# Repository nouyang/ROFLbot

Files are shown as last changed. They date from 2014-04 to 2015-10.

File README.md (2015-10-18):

# Videos

- Lab 1. Wall Find [http://www.youtube.com/watch?v=qMBVbE07Tbg](http://www.youtube.com/watch?v=qMBVbE07Tbg)
- Lab 6. Bulls Eye [https://www.youtube.com/watch?v=fWD04yWnOBU](https://www.youtube.com/watch?v=fWD04yWnOBU)
- Lab 8. Head with potentiometer[ http://www.youtube.com/watch?v=5r9yhMpieDI](http://www.youtube.com/watch?v=5r9yhMpieDI) (position control with motor pot and external pot shown)
- Lab 9. Head with photodiode[ http://www.youtube.com/watch?v=XeEDuTtJMeo](http://www.youtube.com/watch?v=XeEDuTtJMeo)
- Lab 10. Robot with Head [https://www.youtube.com/watch?v=qIvbUR9brPU](https://www.youtube.com/watch?v=qIvbUR9brPU), Rotational Only: [https://www.youtube.com/watch?v=JFF51LcxRAY](https://www.youtube.com/watch?v=JFF51LcxRAY)
- Lab 13. Parking (a) overhead shot (to view any wall-following wobble) [https://www.youtube.com/watch?v=gBMiRD48gqk](https://www.youtube.com/watch?v=gBMiRD48gqk)
     (b) with view of screen / position estimation bars [https://www.youtube.com/watch?v=aKtX0ltPgmw](https://www.youtube.com/watch?v=aKtX0ltPgmw)

# Quickstart
If you have the robot already, simply:

1. Install [lib601](https://github.com/mitocw/mit-6.01-NarwhalEdu-robot/blob/master/lib601.tar.gz) from the 6.01 website.
2. Then replace **/usr/local/lib/python2.7/dist-packages/soar/outputs/pioneer.py** with the NarwhalEdu [pioneer.py](https://github.com/mitocw/mit-6.01-NarwhalEdu-robot/blob/master/code/pioneer.py) 
3. Connect the xbee to the computer
4. Open a terminal and run "dmesg | tail". Note which port is connected -- usually /dev/ttyUSB0 or /dev/ttyACM0.
5. Inside pioneer.py (must be admin to edit this file), edit the line appropriately settings.SERIAL_PORT_NAME = "/dev/ttyUSB1"
6. Run soar from the terminal
7. Click **pioneer** to connect to the robot. If the button stays depressed for a few seconds, that means that you have the right serial port but are having issues connecting to the robot. If it comes depressed right away, check that you edited pioneer.py with the appropriate serial port. If it's connected, it should look like below:

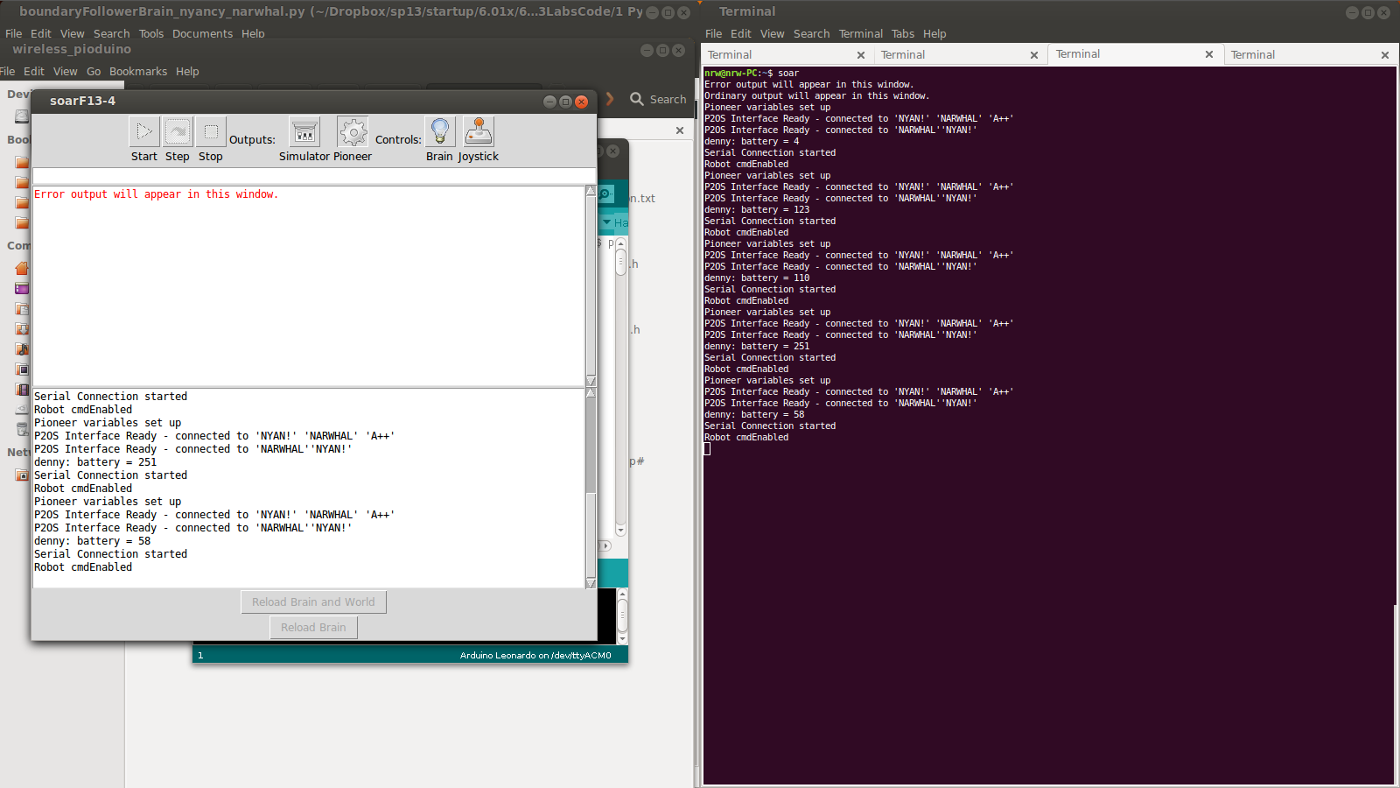
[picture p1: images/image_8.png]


8. If you continue experiencing issues connecting to the robot: hit reset and wait a few seconds (the xbees appear to take a second or two to initialize). Second, try turning the robot on and off. Try replugging the xbee into your computer. Try restarting SOAR. 
9. After it's connected, hit **brain** and load the appropriate brain python file you have written.
10. Hit the square STOP button to stop running the program, and then Reload Brain **and World **if you are going to be moving the robot.

Note:
11. Watch out if the robot ever stops responding or is behaving oddly -- is it still connected to SOAR? and if so, are the batteries low?
12. Other things that are good to check initially -- are the left and right motors mapped in code correctly, are the directions of each motor mapped correctly, are the IR sensors mapped correctly
13. Debugging tip: Robot can be put on top of two wire spools with the casters sitting inside the spools to debug the motors without having it drive all over the place

# Introduction

MIT Office of Digital Learning (ODL) contracted NarwhalEdu to create a
replacement for the robots used in 6.01 as of 2013. 

As of 2013, the Pioneer-DX robots are used, with a head consisting of a
lego motor, a custom 3d-printed chassis, and a custom PCB with two
photodiodes on it.

The motivation for our work was twofold:
1. A smaller robot would allow students to do labs at home
2. A cheaper robot would be more reasonable for online students

In this section, a brief retrospective on the work accomplished and
lessons learned follows, and we end with thoughts about future work. In
the appendix, one may find the proposal we submitted to the ODL.

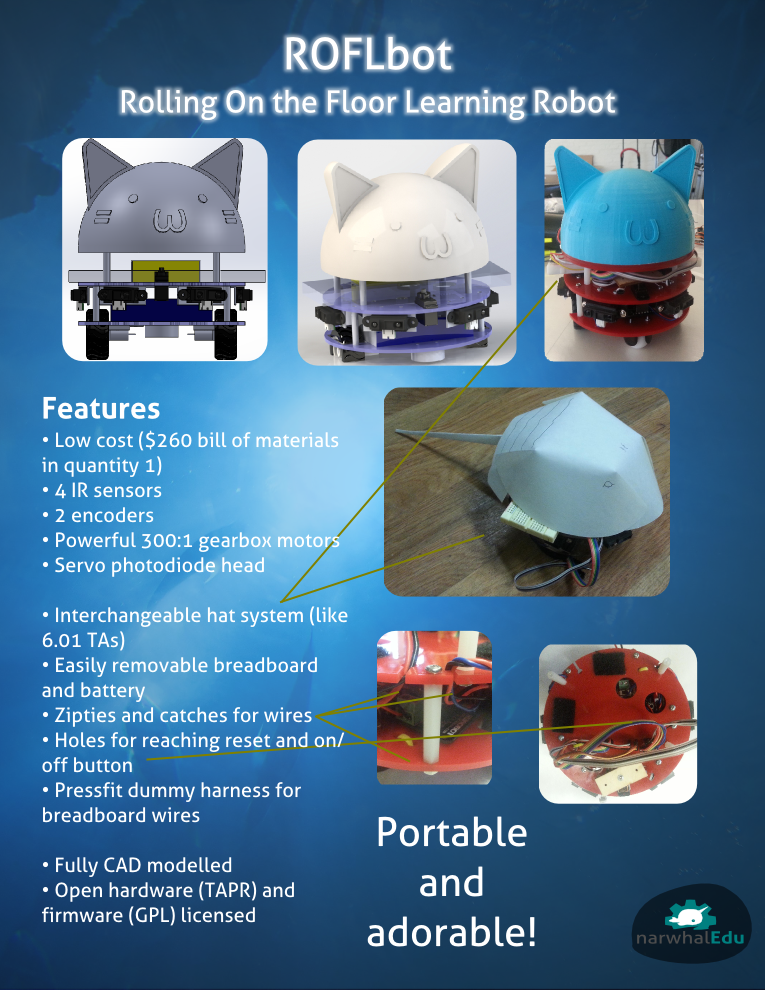
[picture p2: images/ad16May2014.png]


## Who are we?
We’re two engineers from MIT helping students fall in love with
engineering by showcasing its creative side. We're passionate about
increasing the number and diversity of students interested in
engineering around the world, and we hope to bring people together over
the awesome projects that they build.

NarwhalEdu was founded in August 2013 by two MechE '13s: Cappie Pomeroy
and Nancy Ouyang, and ran a successful kickstarter for its first course,
"[Robots, Drawing, and Engineering: An Online
Course](https://www.kickstarter.com/projects/narwhaledu/robots-drawing-and-engineering-an-online-course)," in December 2013.

## Timeline

2013

9/9 Proposal submitted

10/9 Supplies ordered as per invoice

  10/15 PO setup for our work by the ODL

  10/16 Invoice submitted by NarwhalEdu

11/11 Ordered the poorly-documented DFRobot MiniQ robot

  11/17 Check cut

  11/22 Check cashed

2014

1/31 First meeting with Prof. Chuang

2/4 Order gyros, IR distance sensors, Romeo controller board, optical encoders (3.3V by mistake)

2/17 Order 5V optical encoders

2/26 Order 3.3V optical encoders, because they actually work

3/31 Order 300:1 motors, more IR sensors

4/25 1 layer version

5/16 Demo of 2 layer cat head version 

## Summary of Work
In 2013, we evaluated different CPUs, distance sensors, chassis, motors,
and odometry systems. 

We discovered the $79 MiniQ robot, which seemed perfect for our needs,
though it was poorly documented. It was, of course, too good to be true.
The critical two factors were sub-optimal distance and odometry sensing.
In short, we could rig left and right distance sensing, but the sensors
were definitely designed for proximity and not distance sensing. Our
robot was also moving slow enough that we really needed to measure
rotations of the motor, not of the output after the gearbox. (For more
details, see Side Note: Sensors below). However, it did give us the
basis to develop our own robot from scratch and a sense of at what cost
robots could be sold.

As of our first meeting:

CPU: We decided on using Arduino for free and easy-to-use cross-platform
programming toolchain. There was a motor controller - arduino-compatible
board, the Romeo controller, that we found sufficient for our needs.
Distance: We decided on the Sharp IR sensors, since they have a
relatively linear response curve and I knew there was 2.007 code we
could use for them.

Odometry and Chassis: We decided on the pololu round chassis with
high-quality 100:1 gearmotors, since pololu sells them with extended
shafts so that the optical encoders can mount to them. We investigated
gyros but did not end up needing them.

* Note: DFRobot does not sell [knockoff] extended motor brackets that
  cover the gearbox, their "extended" ones are the equivalent of pololu
normal ones, so hair will tend to get caught in them. 

We struggled a lot with the optical encoders. They need thin wires or
else the pads get heat-damaged and fall off. We found servo wires
sufficient for this purpose. Additionally, we bought 3.3V ones by
accident, then bought 5V ones after desoldering a lot of pads, and after
troubleshooting realized that the 5V ones did not generate large enough
signal swing at 5V to trigger the interrupts, but the 3.3 V ones did.

Around this time we also began exploring wireless options, as we found
that the cable to the computer significantly impacted evaluation of the
odometry. Although the previous MiniQ was wirelessly programmable, the
leonardo Romeo board was not. However, this was fine because we learned
that we only needed to wirelessly transmit data. We started with the
xbee, which was the most expensive but the easiest to use given the
pre-existing slot on the romeo. We struggled a lot with the xbee.
Ultimately, a combination of fixing code errors and learning about the
ins and outs of xbees allowed us to create a reliable wireless robot.
(115200 does not exist on the xbee! We ended up using 19200 to avoid any
weird xbee bad rate issues.)

Further work was done to determine that only three IR sensors were
needed to complete the parking lab, however, they had to be
asymmetrically placed. We struggled with the parking lab before
realizing that the real world needed to match the ideal world given to
the robot fairly closely.

### Side Note: MiniQ Documentation
It has
* atmega328p
* cleverly cheap wheel encoders
* spot for an xbee or for the DFrobot Wireless Programming Kit, which
  allows you to wirelessly upload programs
* USB programmable
* a piezo
* lots of LEDs
* pushbuttons
* IRM881T IR receiver that could respond to a keychain remote
* a left and right photoresistor
* two IR LEDs
* 4x ITR2001 optointerupters on the bottom for line-following

### Side Note: Sensors
The IR receiver was a 38kHz receiver. It has a slightly varying response
depending on the strength of the signal received, but in a non-linear
and generally awkward fashion. Conceivably, we could have beeped our two
IR LEDs at 38kHz (alternating, since we only have one receiver, and we
keep track of which are left and which are right) and tried to derive
the distance based on the number of interrupts the IR receiver generates
(DFRobot does provide some sample code that allows you to control the
robot with the remote supplied with the robot), or try short bursts that
get longer and longer until we receive an interrupt, or chirp out a
varying frequency from 36 to 42 kHz and see where we stop getting
interrupts. We could use the photoresistors, but they have slow response
times and wouldn't allow us to modulate at a reasonable frequency so
that we could easily filter out ambient IR. All-in-all, rather
inconvenient, if amazingly cheap. 

We ended up going with the Sharp IR sensors.

The encoder system, developed most likely by pololu originally, worked
thusly: for each wheel, there were two IR20510 light reflection switches
mounted to the chassis. The wheel hub had 12 notches, and as each notch
passed over the switches, it triggered an interrupt. Between the two
reflection switches, this allows the user to treat this system as a
quadrature encoder and be able to detect roughly the speed and whether
the wheel was turning forward or backward. This gives a maximum linear
sensitivity of 3mm. 

See
[http://www.pololu.com/product/1217/resources](http://www.pololu.com/product/1217/resources)
for more information.

This system is cheap and doesn't require any calibration (easy for the
user to assemble), but too low-resolution for our purposes, since we're
always running at low speed. We had difficulty getting the robot to
drive slowly in a straight line with our PID loop. It was limited to 48
ticks per revolution of the wheel, and we had a 100:1 gearbox going at
the time. Ultimately we decided on optical encoders that attached to the
motor shaft directly.

## Details
For more details, see our report on Jan 31, 2014 and on March 11, 2014
in the appendix.

## Future Work
16 May 2014

2 layer robot with interchangeable head system finished.
Immediate fixes recommened: add more holes on top layer to allow access
to motor block terminals on romeo with a screwdriver, lower nut or
otherwise more clearance for USB on romeo (front caster interferes at
the moment), fix fudge factor known as
encodermillimeterconversionfactor (in localization.h) as the motors are
running at lipo voltage ~8v instead of the 5v we thought they were
running at.

25 March 2014

Future work lies in resolving where the breadboard should go and
building a better jig for the head than hot glue, as well as resolving
the photodiode wires into a connector. In the short-term this can
involve a two-layer lasercut chassis with the controller on the bottom
and the breadboard on top. In the future we recommend building the romeo
controller into a custom PCB that serves as the bottom layer and allows
the breadboard layer to be attached with standoffs. This shrinks the
diameter required. Additionally, the optical encoders are finicky in
terms of assembly (they require an oscilloscope to calibrate) and we
hope to replace them with a future product of pololu, magnetic encoder
disks with hall effect sensors that can be integrated into the PCB.
Given a large enough order, a factory can directly create the
control-board-less servo with two tails.

In the future, we recommend better communication between the 6.01 staff
and contractors. Most of our questions were answered by former students
we knew.

13 June 2014
Future work will probably lie in migrating away from the optical
encoders, which are really annoying to calibrate. Additionally, we need
to pick a license and also publish the hardware and firmware to a
publicly accessible repository. The code examples need to be refined,
especially roverBrain, to work consistently. A better holder (hinged)
for the interchangeable heads would be great as well.

## BoM
All prices in USD and as of March 2014.
                                             
<table>
  <tr>
    <td>Name</td>
    <td>Total Cost</td>
    <td></td>
    <td>Product Name</td>
    <td>URL</td>
  </tr>
  <tr>
    <td>Custom Lasercut Chassis (based on pololu)</td>
    <td>$7.95</td>
    <td>pololu</td>
    <td>#1507 Pololu 5" Robot Chassis RRC04A Transparent Light-Blue</td>
    <td>http://www.pololu.com/product/1507</td>
  </tr>
  <tr>
    <td>Lipo Battery Connector</td>
    <td>$0.99</td>
    <td>pololu</td>
    <td>JST RCY Plug with 10cm Leads, Male</td>
    <td>http://www.pololu.com/product/2181</td>
  </tr>
  <tr>
    <td>Lipo Battery</td>
    <td>$4.65</td>
    <td>hobbyking</td>
    <td>Turnigy 1000mAh 2S 20C Lipo Pack</td>
    <td>http://www.hobbyking.com/hobbyking/store/__9170__Turnigy_1000mAh_2S_20C_Lipo_Pack.html</td>
  </tr>
  <tr>
    <td>4x Sharp IR Sensor</td>
    <td>$39.80</td>
    <td>pololu</td>
    <td>#136 Sharp GP2Y0A21YK0F Analog Distance Sensor 10-80cm</td>
    <td>http://www.pololu.com/product/136</td>
  </tr>
  <tr>
    <td>3x Sharp IR mount</td>
    <td>$15.00</td>
    <td>robotmesh</td>
    <td>Sharp IR Sensor Mounting Bracket-GP2Y0A21/GP2Y0A02YK</td>
    <td>http://www.robotmesh.com/sharp-ir-sensor-mounting-bracket-gp2y0a21-gp2y0a02yk?___SID=U</td>
  </tr>
  <tr>
    <td>10x bolts for IR mount, mcu</td>
    <td>$1.63</td>
    <td>mcmaster</td>
    <td>Zinc-pltd Stl Pan Head Phillips Machine Screw, 4-40 Thread, 1/2" Length x 100</td>
    <td>http://www.mcmaster.com/?error_redirect=true#90272a110</td>
  </tr>
  <tr>
    <td>10x nuts for IR mount, mcu</td>
    <td>$0.81</td>
    <td>mcmaster</td>
    <td>Zinc-plated Steel Machine Screw Hex Nut, 4-40 Thread Size, 1/4" Width, 3/32" Height x 100</td>
    <td>http://www.mcmaster.com/?error_redirect=true#90480A005</td>
  </tr>
  <tr>
    <td>2x 300:1 Gearmotor</td>
    <td>$33.90</td>
    <td>pololu</td>
    <td>#2218 298:1 Micro Metal Gearmotor HP with Extended Motor Shaft</td>
    <td>http://www.pololu.com/product/2218</td>
  </tr>
  <tr>
    <td>42x19mm Wheel, pair</td>
    <td>$3.85</td>
    <td>robotmesh</td>
    <td>Wheel 42x19mm (Pair)</td>
    <td>http://www.robotmesh.com/wheel-42x19mm-pair</td>
  </tr>
  <tr>
    <td>Extended Motor Bracket, Pair</td>
    <td>$2.99</td>
    <td>pololu</td>
    <td>#1089 Pololu Micro Metal Gearmotor Bracket Extended Pair</td>
    <td>http://www.pololu.com/product/1089</td>
  </tr>
  <tr>
    <td>2x Optical Encoder</td>
    <td>$17.90</td>
    <td>pololu</td>
    <td>#2591 Optical Encoder Pair Kit for Micro Metal Gearmotors, 3.3V</td>
    <td>http://www.pololu.com/product/2591</td>
  </tr>
  <tr>
    <td>2x Caster</td>
    <td>$9.98</td>
    <td>Robotmesh</td>
    <td>#956 Pololu Ball Caster with 1" Plastic Ball</td>
    <td>http://www.pololu.com/product/956</td>
  </tr>
  <tr>
    <td>8x Standoff</td>
    <td>$2.00</td>
    <td>Robotmesh</td>
    <td>10 sets M3 * 30 nylon standoffs</td>
    <td>http://www.robotmesh.com/10-sets-m3-30-nylon-standoffs</td>
  </tr>
  <tr>
    <td>7x 3 wire</td>
    <td>$6.00</td>
    <td>Robotmesh</td>
    <td>Analog Sensor Cable For Arduino (10 Pack)</td>
    <td>http://www.robotmesh.com/analog-sensor-cable-for-arduino-10-pack</td>
  </tr>
  <tr>
    <td>Romeo Controller</td>
    <td>$39.90</td>
    <td>Robotmesh</td>
    <td>Romeo V2-All in one Controller</td>
    <td>http://www.robotmesh.com/romeo-v2-all-in-one-controller</td>
  </tr>
  <tr>
    <td>Head Servo</td>
    <td>$5.00</td>
    <td>Emax</td>
    <td>ES08DE Digital Servo</td>
    <td>http://www.emaxmodel.com/views.asp?hw_id=1247</td>
  </tr>
  <tr>
    <td>Long Servo Extension Cable</td>
    <td>$0.7</td>
    <td>Robotmesh</td>
    <td>Servo Extension Cable 300mm</td>
    <td>http://www.robotmesh.com/servo-extension-cable-300mm</td>
  </tr>
  <tr>
    <td>10 flexible wires</td>
    <td>$1.5</td>
    <td>amazon, ebay</td>
    <td>40 Pin M/M Color Ribbon Solderless Breadboard Cable 2.54mm 20cm</td>
    <td></td>
  </tr>
  <tr>
    <td>1x washer</td>
    <td>$1.19</td>
    <td>Mcmaster</td>
    <td>Zinc-Plated Steel Type A SAE Flat Washer, Number 2 Screw Size, 7/32" OD, .01"-.03" Thick</td>
    <td>http://www.mcmaster.com/?error_redirect=true#90126A501<td>
  </tr>
  <tr>
    <td></td>
    <td></td>
    <td></td>
    <td>Subtotal</td>
    <td>$193.05</td>
  </tr>

  <tr>
    <td></td>
    <td></td>
    <td></td>
    <td></td>
    <td></td>
  </tr>
  <tr>
    <td>Wireless</td>
    <td></td>
    <td></td>
    <td></td>
    <td></td>
  </tr>
  <tr>
    <td>2x Xbee</td>
    <td>$41.90</td>
    <td>Robotmesh</td>
    <td>XBee 1mW Trace Antenna - Series 1 (802.15.4)</td>
    <td>http://www.robotmesh.com/xbee-1mw-trace-antenna-series-1-802-15-4</td>
  </tr>
  <tr>
    <td>Xbee USB Adapter</td>
    <td>$18.50</td>
    <td>Robotmesh</td>
    <td>XBee USB Adapter V2</td>
    <td>http://www.robotmesh.com/xbee-usb-adapter-v2</td>
  </tr>
  <tr>
    <td>USB Mini Cable</td>
    <td>$1.90</td>
    <td>Robotmesh</td>
    <td>Mini USB cable</td>
    <td>http://www.robotmesh.com/mini-usb-cable</td>
  </tr>
  <tr>
    <td></td>
    <td></td>
    <td></td>
    <td>Total</td>
    <td>$256.85</td>
  </tr>
  <tr>
    <td>Misc.</td>
    <td></td>
    <td></td>
    <td></td>
    <td></td>
  </tr>
  <tr>
    <td>1'' strip of velcro</td>
    <td></td>
    <td></td>
    <td></td>
    <td></td>
  </tr>
  <tr>
    <td>3x zipties</td>
    <td></td>
    <td></td>
    <td>tiny 4'' ones</td>
    <td></td>
  </tr>
  <tr>
    <td>lipo charger</td>
    <td></td>
    <td></td>
    <td></td>
    <td></td>
  </tr>
  <tr>
    <td>3d printed head</td>
    <td></td>
    <td></td>
    <td></td>
    <td></td>
  </tr>
  <tr>
    <td>breadboard</td>
    <td></td>
    <td></td>
    <td></td>
    <td></td>
  </tr>
  <tr>
    <td>IR photodiodes</td>
    <td></td>
    <td></td>
    <td>Silonex SLD-701R2A</td>
    <td>http://sicp-s4.mit.edu/cat-soop/6.01_S14/circuits</td>
  </tr>
</table>

## Assembly Instructions
See bill of materials for needed parts. Additionally, wire strippers, #0 and #1 phillips screwdriver, a #0 slotted screwdriver, tape, hot glue gun, and soldering iron needed. We also recommend having flush cutters in case of ziptie mishaps.

### Lasercut Chassis Parts
Cut out the files below:

1. Out of 3mm acrylic (any color, black or slightly transparent blue
   recommended), the coreldraw file:
[chassis](https://github.com/mitocw/mit-6.01-NarwhalEdu-robot/blob/master/hardware/lasercut/12June2014.cdr)
2. Out of 3mm acrylic, the inkscape file: [pressfit servo
   horn](https://github.com/mitocw/mit-6.01-NarwhalEdu-robot/blob/master/hardware/lasercut/servohorn.svg)

### Wiring Diagram
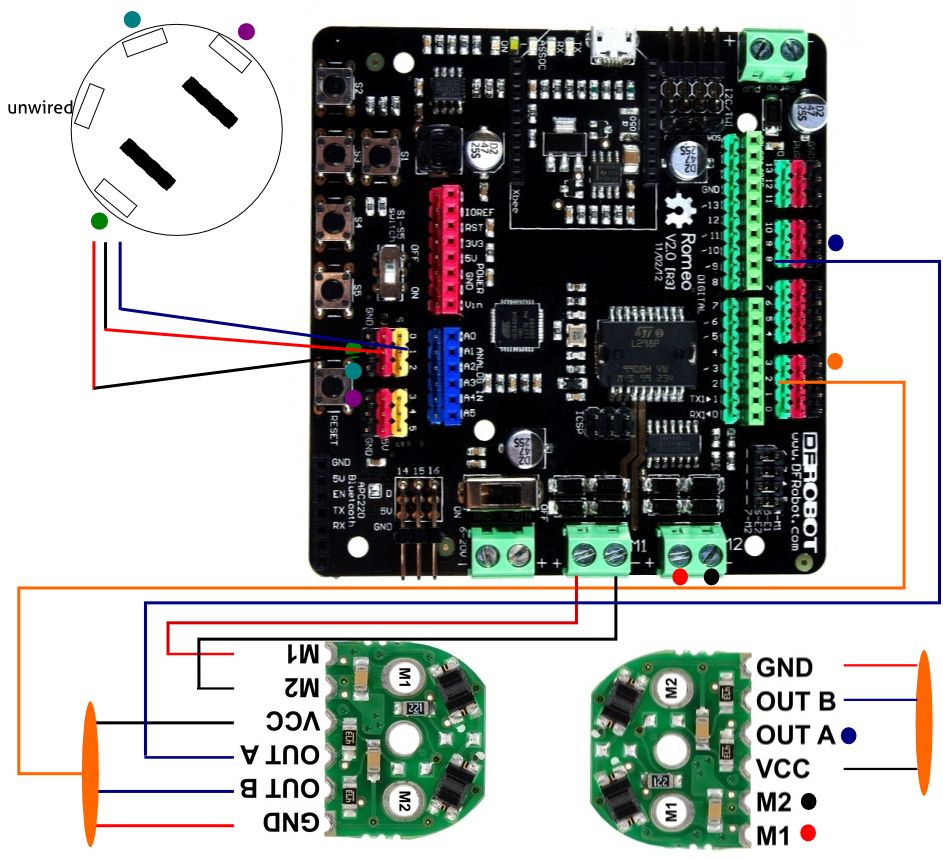
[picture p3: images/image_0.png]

Note: above picture out of date due to move to four sensors instead of
three, see "sensor unit assembly" for revised analog pin connections.

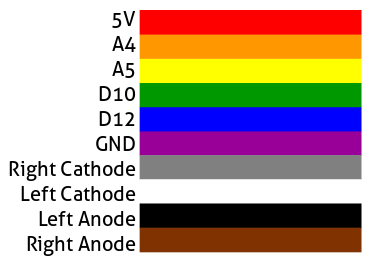
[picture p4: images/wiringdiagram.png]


### Wiring Picture
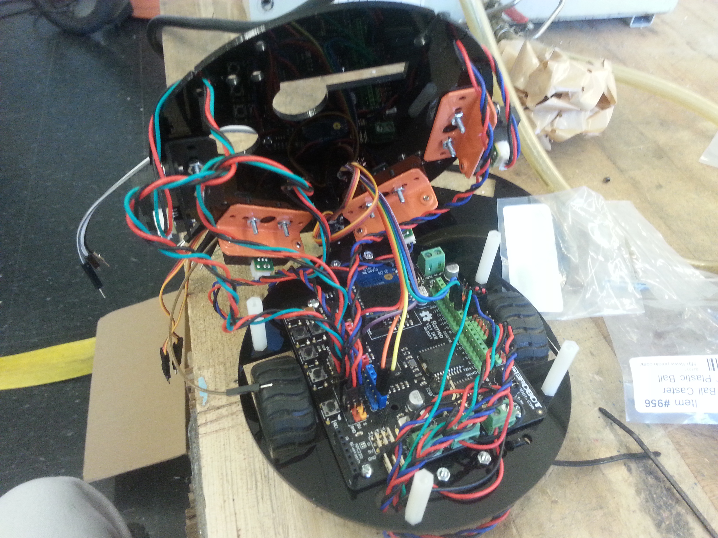
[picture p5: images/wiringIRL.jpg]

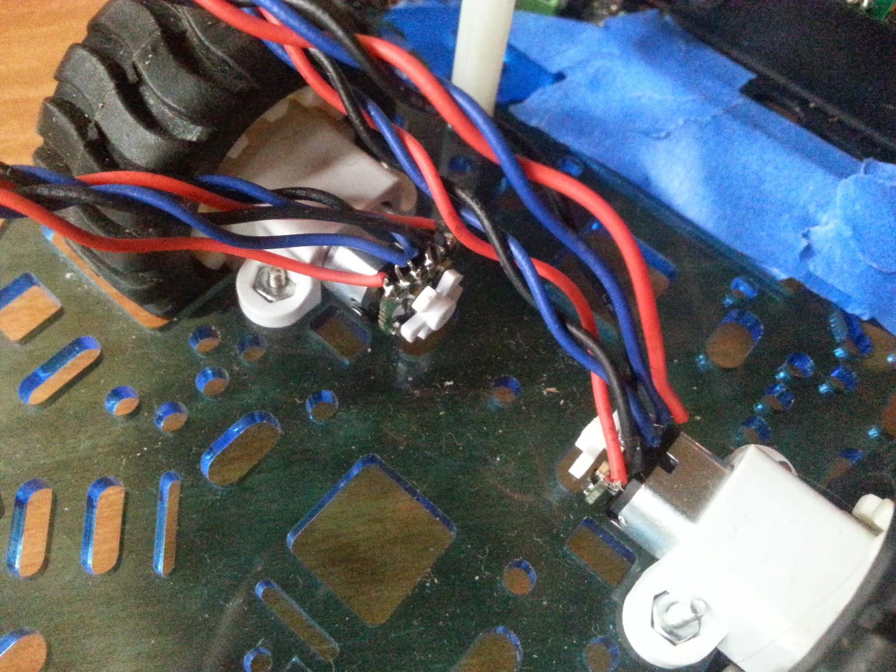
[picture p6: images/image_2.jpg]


### Step-by-step Instructions

**Motor Unit Assembly**

1. Solder optical encoder to motor. Try to make sure the IR sensors are an equal distance from the motor back end, that way as the white encoder disc spins they are triggered equally.
2. Strip two of the 3-wires. Solder them to the as in the picture above -- red1-blue1-blue2-black1-black2. 
Future wiring notes:
 1. 3-wire number 1 will be plugged into one of the digital pin breakouts
 2. 3-wire number 2 will be plugged into another digital pin and then the black and red wires on it will be cut, stripped, and put into the motor output terminals on the romeo
3. Tune with oscilloscope and plastic screwdriver until the bottom of the waveform dips to zero (below 0.2V) (or else it won't trigger the interrupt as a V_low) (see [http://www.pololu.com/product/2590](http://www.pololu.com/product/2590) for more details)
4. Put motor bracket on motor
5. Put wheel on motor shaft
6. Repeat for other motor

**Sensor Unit Assembly**

1. Screw IR sensor onto L-shaped IR mount
2. Swap the red and black wires by pressing on the plug with the tiny slotted screwdriver and pulling the red and black wires out, then reinserting them swapped with each other on the 3-wire analog connector (this is because the romeo controller goes  SIG 5V GND instead of the SIG GND 5V that the IR sensors wants).
3. Bolt sensor assembly onto the bottom of the top chassis piece. 



3. Later step: Plug the leftmost sensor into analog pin 0, center-left into analog pin 1, center-right into analog pin 2, and the right sensor into analog pin 4.

**Servo Head Assembly**

1. Take off bottom part of case (unscrew 4 screws with a #0 screwdriver)

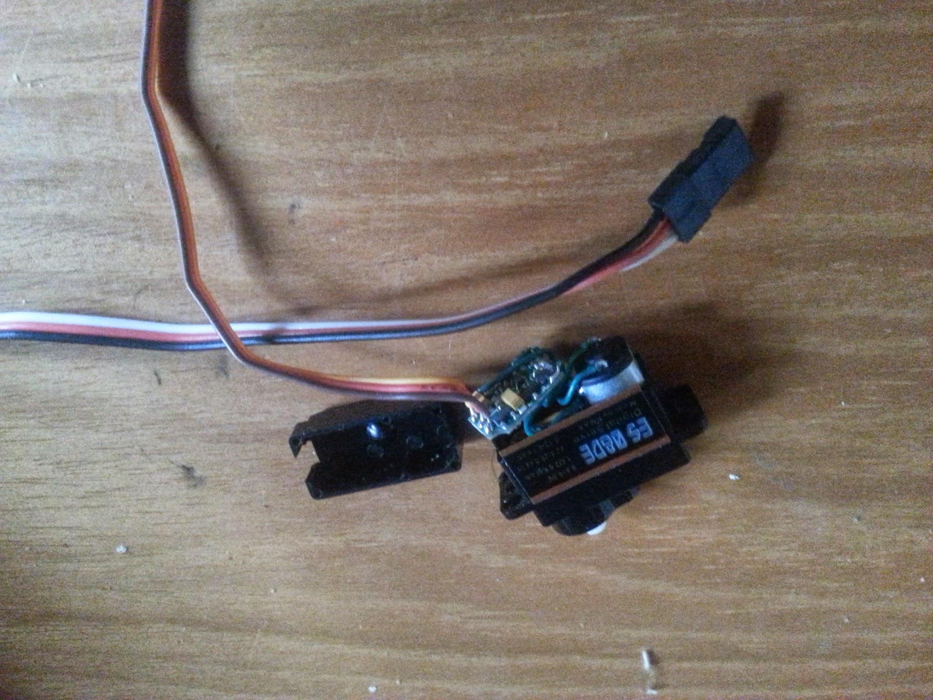
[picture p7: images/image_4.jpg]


2. Desolder control board
3. Resolder 3-wire leads to motor. Mark which wires go to the motor with
   an "M" on female plug. The red wire should be the slider on the pot.
4. Cut and strip a new 3-wire (ideally a servo extension cable, the analog cables are fine electrically but physically may not lie flat enough to exit the servo case smoothly)
5. Solder 3-wire leads to potentiometer

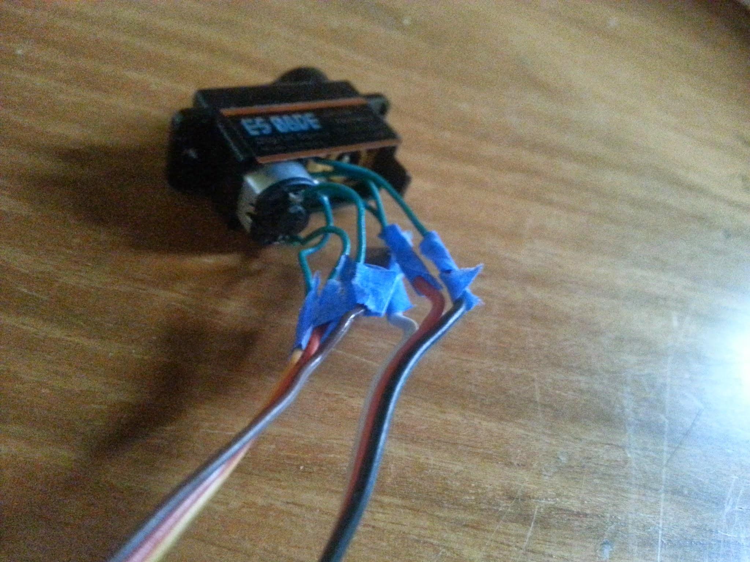
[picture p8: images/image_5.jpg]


6. Place leads appropriately so that you can put the case back on

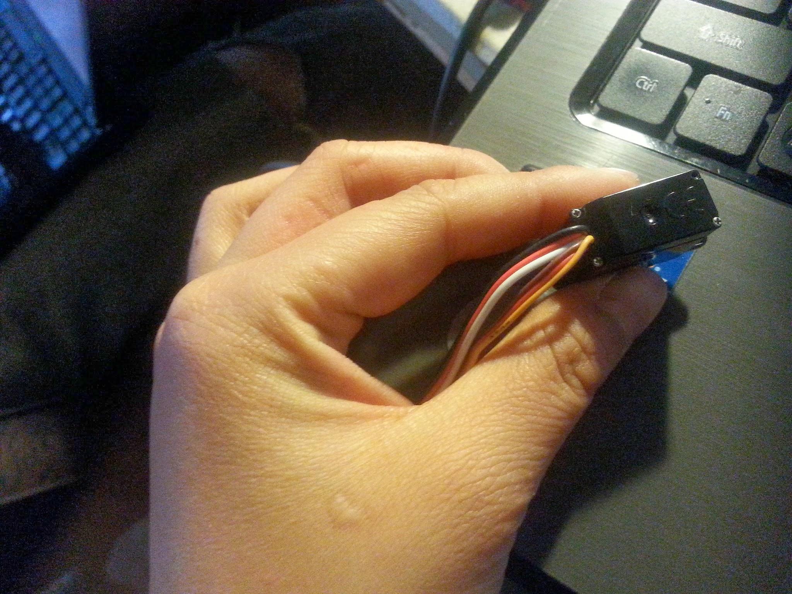
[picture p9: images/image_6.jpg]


8. Solder wires to the photodiodes as show in the picture below (black and brown wires going to the side with the red dot), then hotglue the photodiodes down to the lasercut servohorn piece such that they are facing 90 degrees apart from each other. See picture below.

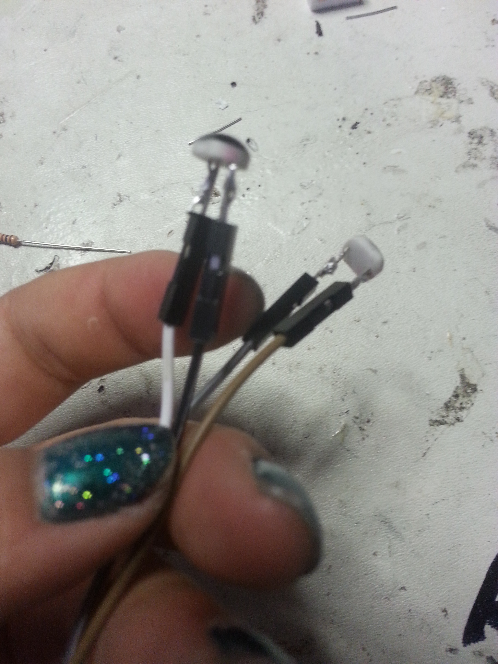
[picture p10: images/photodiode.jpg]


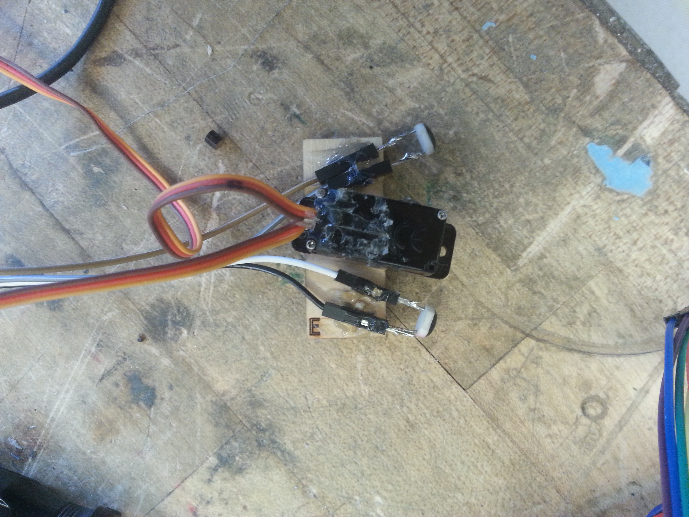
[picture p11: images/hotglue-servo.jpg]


8. Attach the lasercut wooden piece to the servo with a short screw
   (comes with servo) and a washer.

9. Attach the lasercut wooden piece the top chassis piece with two
   shoulder flange screws (the longer ones that come with the servo).

**Robot Assembly**

1. Screw motor bracket with motor down to bottom of chassis, along with the thin
   shims for the motor, with the 4-40 bolts and nuts.
3. Screw casters onto bottom of chassis (there should be two casters, on up front and one in the back)
4. Put tape on top of bolts sticking out the top from the motors. 

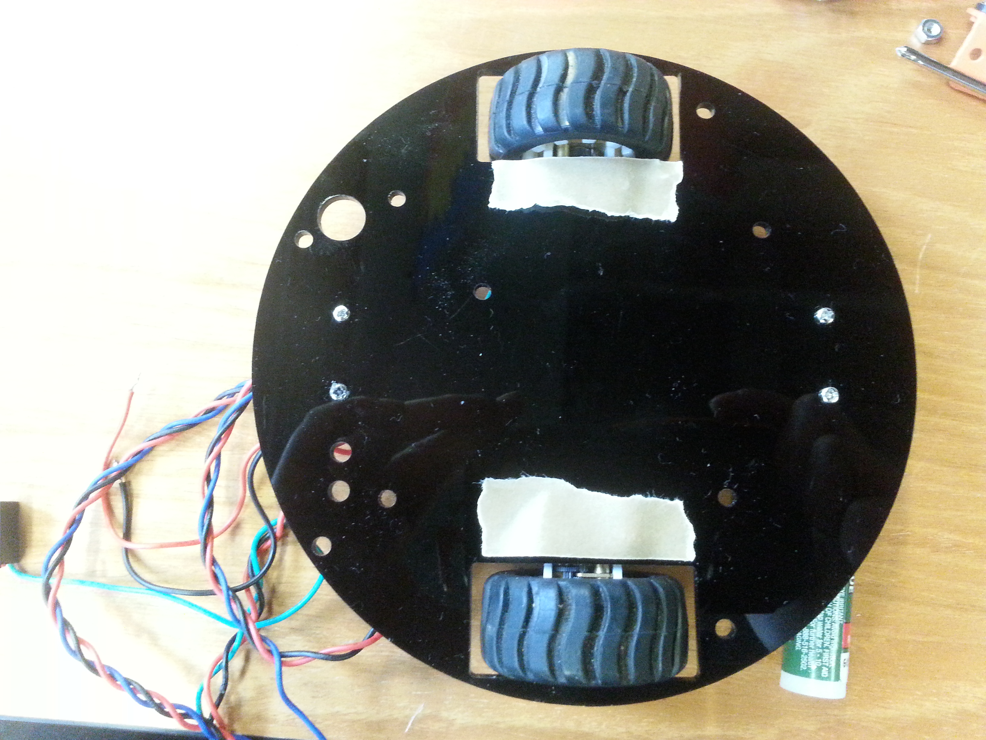
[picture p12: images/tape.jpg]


4. Screw romeo controller to top of bottom piece of chassis. Attach
   wires from motor after zip-tieing appropriately. See wiring diagram.

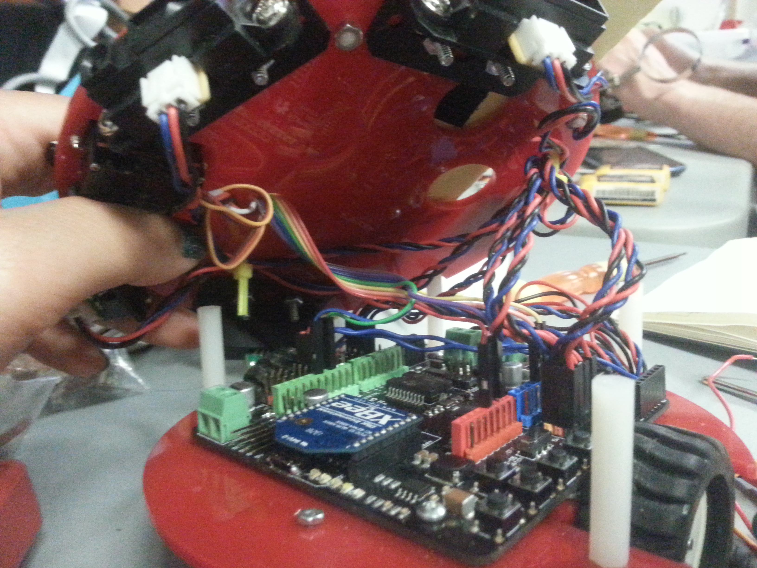
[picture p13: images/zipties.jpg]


4. Plug in IR sensors and the rainbow wire as according to wiring diagram. Ziptie appropriately.
Make sure to route left and right IR sensor wires into the holes on the
top chassis to secure them from rubbing against the wheels.

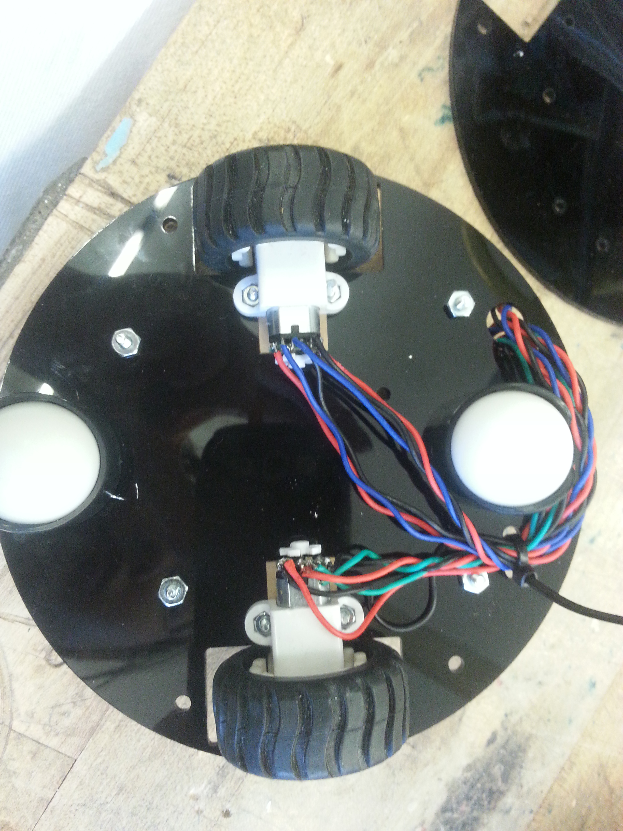
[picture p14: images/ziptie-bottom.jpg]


4. Screw all the standoffs to chassis (both pieces)
4. Attach the top piece to the bottom piece chassis-wise. 
4. Attach velcro to the top of the top chassis and the bottom of the
   breadboard and the battery. Place breadboard and battery. Route
battery cable through hole for it.

**Program Xbees**

1. Boot into windows and install XCTU. It is a large piece of software.
2. Program the xbees to talk to each other (DL and MY commands)
   1. Plug one xbee into a USB explorer and connect to computer
   2. Under Device Manager, note which serial port 
   3. Click "Add'
      1. Serial port: use the one noted in Device Manager
      2. If factory xbee, try 9600 baud rate. Otherwise, try the last baud rate you remember, and otherwise just try process of elimination
  4. Click on the device
  5. **Change DL and MY appropriately. e.g. for xbee1, you can set MY=1111 and DL=2222. Then for the other xbee, you would set MY=2222 and DL=1111.**
  6. Set the **baud rate to 19200**
  7. Make sure the channel and pan id are the same for both devices
  8. Optionally, set the node identifier (some human-recognizable name)
  9. The software is a little buggy, if you cannot get rid of the DH (set it to zero) after accidentally setting it to something nonzero, go into the console tab, hit connect
      1. Add a packet -- "+++" .
      2. Send selected packet -- you should get an "OK" in response letting you -know the device is awake. Note that the device falls asleep fairly quickly.
      3. Add packet -- "ATMY[enter]" (the enter is important!). Send it. You should receive the current MY back.
      4. To change the DH, add a packet -- "ATDH0[enter]" and send it. You should get "OK" back.
      5. Add a packet -- "ATWR[enter]" and send it. You should get an "OK" back. **This writes changes to flash.**
      6. You can hit disconnect, unplug and re-plug in the xbee, reconnect it, and let XCTU read all the values to double-check that you changed the value you wanted to change.

**Robot Wiring**

1. Cut and strip two leads on one of the 3-wires for the motor
2. Plug in / screw leads for motor to M1/M2 and digital pins
3. Plug in IR sensor to analog input pins
4. Plug in Xbee
5. Screw in JST 2-wire XH-style lipo male connector
6. Plug-in battery

**Program Arduino**

1. Install the Arduino IDE by following the directions [here](http://arduino.cc/en/Guide/HomePage).  If you're using Ubuntu I recommend getting the .debs from Debian Sid outlined near the bottom of [this page](http://playground.arduino.cc/Linux/Ubuntu).  They are more up to date.  You need Arduino version 1.0.1 or greater to program the Arduino Leonardo
2. Download the [wireless_pioduino folder](https://github.com/mitocw/mit-6.01-NarwhalEdu-robot/tree/master/code/wireless_pioduino).  Open up [wireless_pioduino.ino](https://github.com/mitocw/mit-6.01-NarwhalEdu-robot/blob/master/code/wireless_pioduino/wireless_pioduino.ino).
3. Select Tools>Board>Arduino Leonardo and Tools>Serial Port>YOUR\_ARDUINO\_PORT \(to find YOUR\_ARDUINO\_PORT\ on Linux just plug in the Arduino, go to a terminal and enter `dmesg | tail` the Arduino Leonardo should show up as `/dev/ttyACMx` where x is usually `0` or `1`)
4. Hit upload
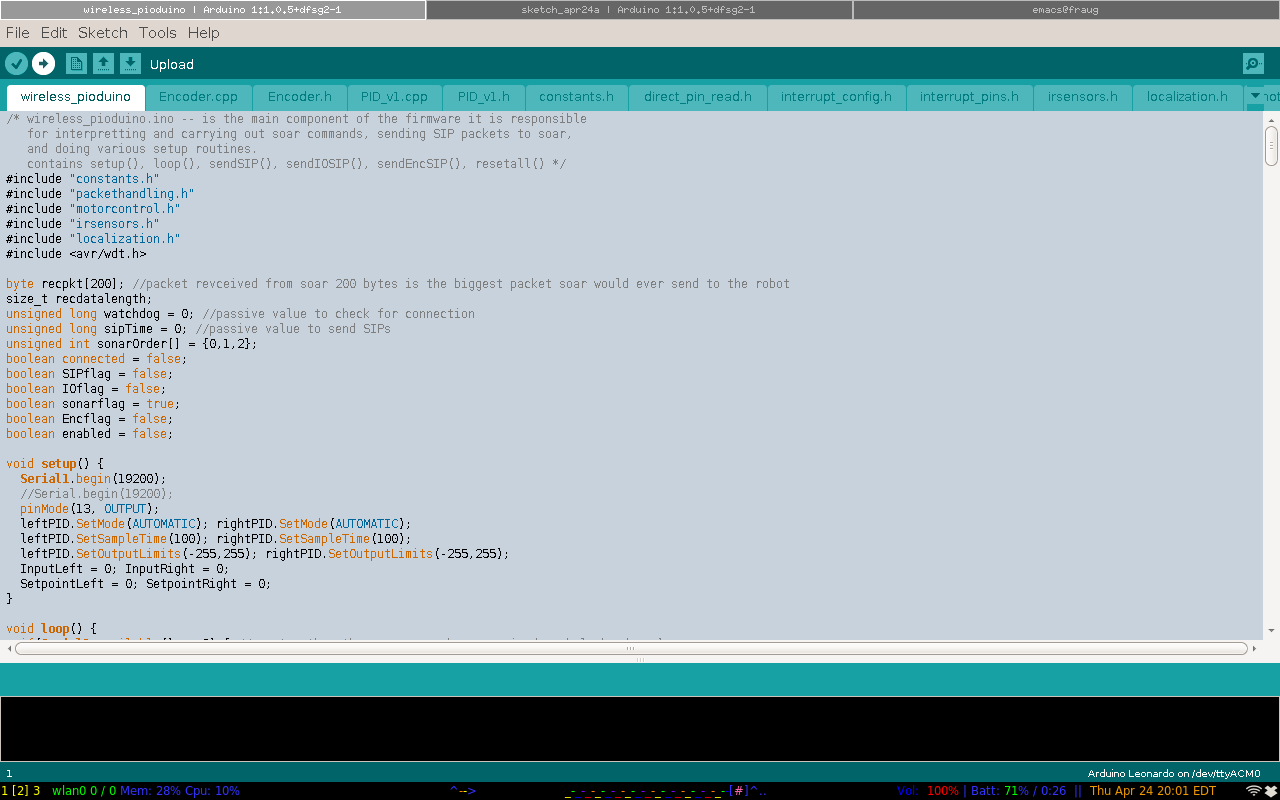
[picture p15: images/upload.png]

5. The Leonardo should blink its lights as the program is uploading once it's done the robot is ready to go.  Sometimes the upload fails on the first try this seems to be a common problem with the Leonardo.

## Software

See the "Quickstart" section at the very beginning of this document.

# SOAR

Only [pioneer.py](https://github.com/mitocw/mit-6.01-NarwhalEdu-robot/blob/master/code/pioneer.py) was modified, sonarDist should be modified (discussed below)
We altered pioneer.py in the following ways:

1. `MAX_TRANS` now equals 0.2
2. `RADIAN_SCALE` now equals pi/180
3. `sonarsChanged`, `storedsonars`, `oldsonars`, `changed`, and `sonars` are now only size 3
4. `baudRates` to include 19200
5. `timeout` to 0.5
6. the missed packets criteria (`self.zero_recv_cnt`) to be 100 which is ~25 lost packets
7. `bufferidx `is now 4 (because IO packet size changed)
8. analog inputs are multiplied by 5/1023 instead of 10/1023 because system voltage is only 5
9. stallbump is no longer in the SIP packet, so all lines relating to that are commented out
10. SIP packet changed size so all numbers within it are different

# Code Changes

-> sonars are numbered differently

The only change to how the lab code is written is the sonar numbering.  There are only 3 sonars so `inp.sonars` and `io.getSonars()`will only return a list of length 3.  The convention is the same with `sonar[0]` being the most left and the index increasing as you go right.  `sonarMax` should be only ~0.80m that’s the range of the IR sensors in the spec sheet.

The only internal function used we found that fails because of this difference is `getDistanceRightandAngle()`, but other functions that we didn’t come across may also have errors.  Here’s the code we used in place of it, but presumably you can just edit sonarDist to correct the indices and and spacing of sensors.  In our case, we measured 65 degrees between the right sensor and right-center sensor.

```python
def getDistanceRightAndAngle(s):
    angleSpaced = 65*math.pi/180
    right = s[2]
    center = s[1]
    sonarMax = 0.8
    if right < sonarMax and center < sonarMax:
        radius = 0.089/2
        a = center+radius
        b = right+radius
        c = math.sqrt(a*a+b*b-(2*a*b*math.cos(angleSpaced)))
        phi = math.asin((a/c)*math.sin(angleSpaced))
        if phi > math.pi/2:
                d = b*math.sin(phi-math.pi/2)
                  alpha = math.acos(d/b)
                theta = -alpha
        else:
                d = b*math.sin(phi)
                if d/a > 1:
                    return(right,None)
                alpha = math.acos(d/a)
                   theta = alpha-angleSpaced
        return(d,theta)
    elif right < sonarMax:
            return(right, None)
    elif center < sonarMax:
            return(center, None)
    else:
            return(sonarMax, None)
```

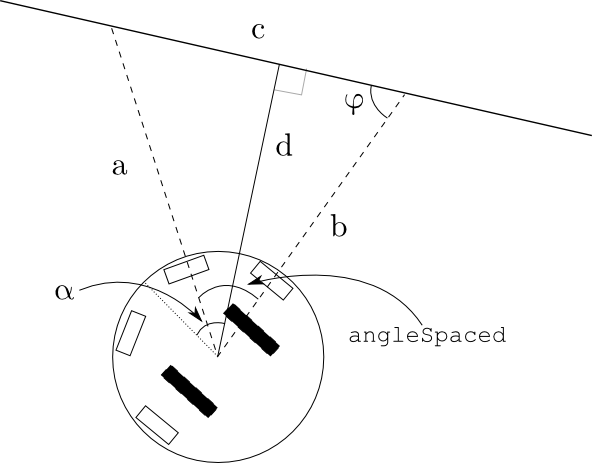
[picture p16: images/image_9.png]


**Differences from Pioneer OS:**

Basically, the Arduino is running a much simpler pioneer OS v3.  

* All the commands that 6.01 seems to use currently were implemented.  Many of the rest are empty case statements.
* There are ~5960 encoder ticks per revolution of the wheels
* Since soar ignores a lot of the information in SIP packets and to improve wireless communication the SIP packets were reduced in size the standard SIP only sends position and sonar information so its maximum size is 17 bytes.  The IO SIP is also only 17 bytes but only bytes 0 and 9-14 (numbering excludes header) are nonzero, the others were left in in case more analog inputs would need to be used but currently I believe soar ignores them.
* Again there are only 3 IR sensors not 8.  Each reported reading is the average of 5 values taken from the sensor.

# Labs

### Lab 1

Part 1. Robot maintains distance from a foamboard wall in front of it.

1. Load the [boundaryFinder brain](https://github.com/mitocw/mit-6.01-NarwhalEdu-robot/blob/master/code/designLab01/boundaryFinderBrain_narwhal.py).
2. Move foamcore backwards and forwards. Robot should follow it (even though there is no center IR sensor, we use the center-right one and it is sufficient).

Part 2. Robot maintains distance from a wall on the right-hand side.

1. Load the [boundaryFollower brain](https://github.com/mitocw/mit-6.01-NarwhalEdu-robot/blob/master/code/designLab01/boundaryFollowerBrain_narwhal.py).
2. Set the foamcore upright on the right-hand side of the robot. Hit
   play.

### Lab 6

1. Setup a foamcore wall on the right side
2. Set the robot 0.4 meters from the wall, rotated at about pi/8. 
3. Set the bulls eye (created out of foam and a paperclip) up about 1
   meter in front of the robot, 0.3 meters from the wall.
4. Tape a pen to the top of the robot.
5. Load the [angle brain](https://github.com/mitocw/mit-6.01-NarwhalEdu-robot/blob/master/code/designLab06/angleBrain_narwhal.py) and hit run. Robot should go towards the wall, reach
   its desired distance from the wall, and then follow the wall until
   it lances the bullseye.
6. Adjust the height of the bullseye as needed.

Brain-wise, kp = 10 and ka = 1.99899 work well with desiredRight = 0.3.

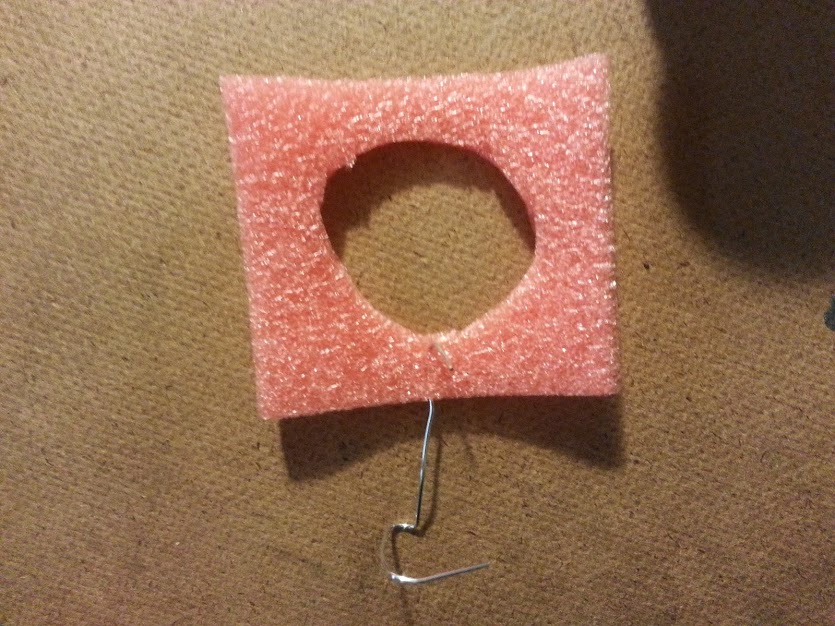
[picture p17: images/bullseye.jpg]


### Lab 8

Use male headers to connect motor and potentiometer to breadboard as appropriate. Note that the 10V source in all the following diagrams is replaced by a 5V source. **Use the L272 op-amp (****[http://sicp-s4.mit.edu/cat-soop/6.01_S14/circuit**s](http://sicp-s4.mit.edu/cat-soop/6.01_S14/circuits)**) as it is capable of sourcing enough current for this application.**

Section 4.2 Checkoff 1: Buffered potentiometer divider circuit, Control motor speed with potentiometer (single direction)

* Materials: breadboard, 5V from the romeo board, pot, L272 op-amp, and motor

* 

Section 5 Checkoff 2: Bidirectional Speed Controller, Control motor speed with pot (bidirectional)

Build this circuit:

* Materials: breadboard, 5V from the romeo board, pot, L272 op-amp, two equivalent value resistors probably of at least 5k, and motor

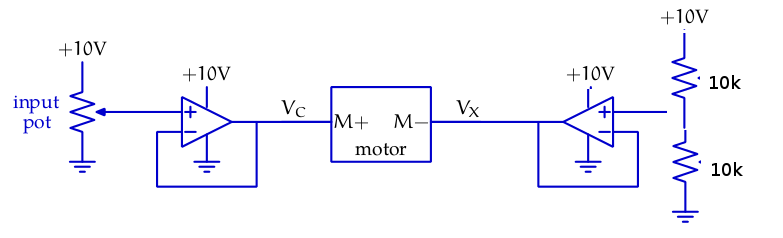
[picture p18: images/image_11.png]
* 

Section 6 Checkoff 3: Angular Position Controller, Control motor angle with pot

* Materials: breadboard, 5V from the romeo board, pot, L272 op-amp, a servomotor

* Simply replace the voltage divider circuit in the previous part of the lab with the potentiometer output from the servomotor.

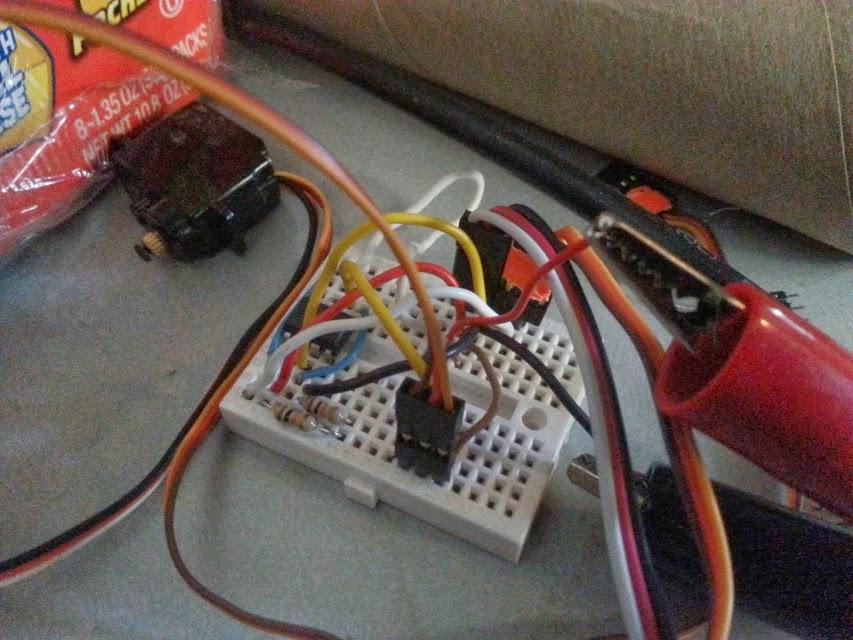
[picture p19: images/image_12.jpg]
*  
(the output from the voltage divider in this picture is not being used, the resistors just haven't been pulled out)

### Lab 9

To create a head that tracks light, we use the output from two Silonex SLD-701R2A IR photodioes. A circuit such as below would work:

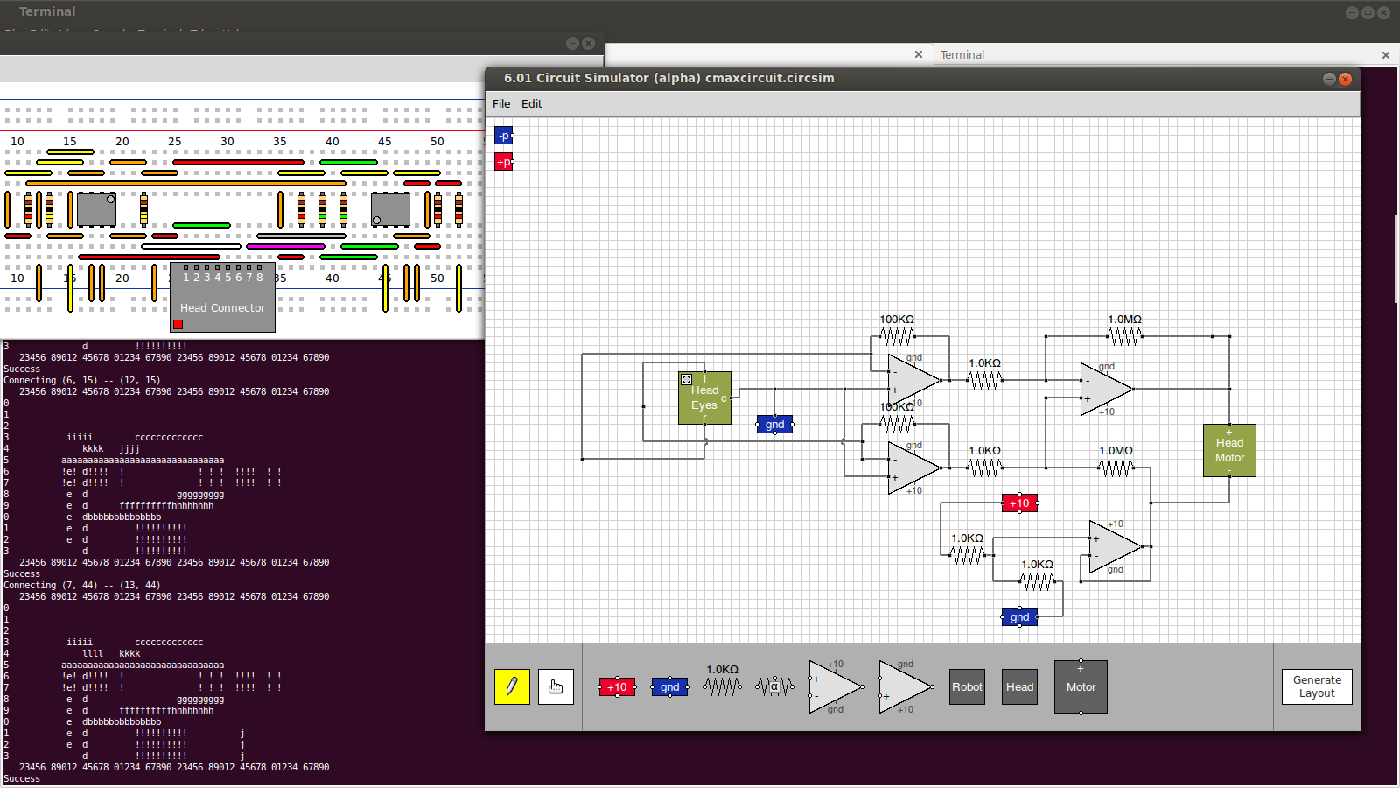
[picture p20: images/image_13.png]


Namely, two transimpedance amps to convert current from the photodiodes into voltage, fed into a differential amplifier, that is then fed to the motor. On the other side of the motor we have the standard voltage divider circuit circuit fed into a buffer that is then fed into the motor.

If you have issues with the head railing to one side when there is no direct light source, **check the gains** on the transimpedance amps. The gains may be too high and the op-amps are hitting their rails.

Note: Use 330K instead of 1M on the differential amplifer or else the head will rail to one side when no light is present.  330K is the largest standard resistor that can be used without railing

### Lab 10

This lab requires a fairly intense IR source (a lamp works, we haven't
tried it with IR keychains yet). 

1. Connect the servomotor potentiometer lead to power, ground, and to
   analogPin10 (labeled 10). Connect the left photodiode voltage (output of the
   transimpedance amp) to analogPin4 (labeled A4), and the right one to analogPin5 (labeled A5).
   Connect 5V and GND to the breadboard rails from the controller.

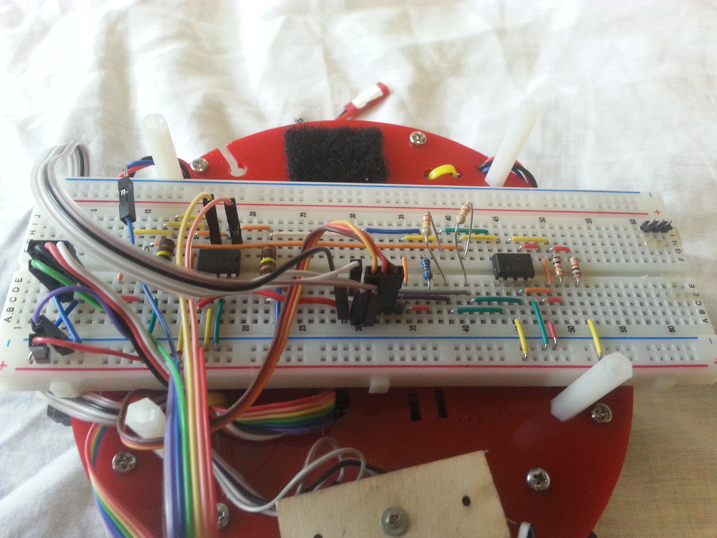
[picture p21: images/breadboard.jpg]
 

2. Load the [rover brain](https://github.com/mitocw/mit-6.01-NarwhalEdu-robot/blob/master/code/designLab10/roverBrain_narwhal.py). Run it. The robot should attempt to maintain a
   distance from the light by both following and retreating, as well as
   maintaining its position when there is no light.  
3. Values in the code that will depend on the light source: the exact thresholds for
   the photodiode voltages (to find these, just print out the IR
   readings vLeft and vRight and move the light around while commenting out
   all the setForwards that are non-zero)
   Note that the code is written in a way that when it decides the light is
   too close, it will rapidly move away from it and then slowly move
   away from it. This is just the way we chose to implement the lab.

Here's a graph of the photodiode output using a big lamp.

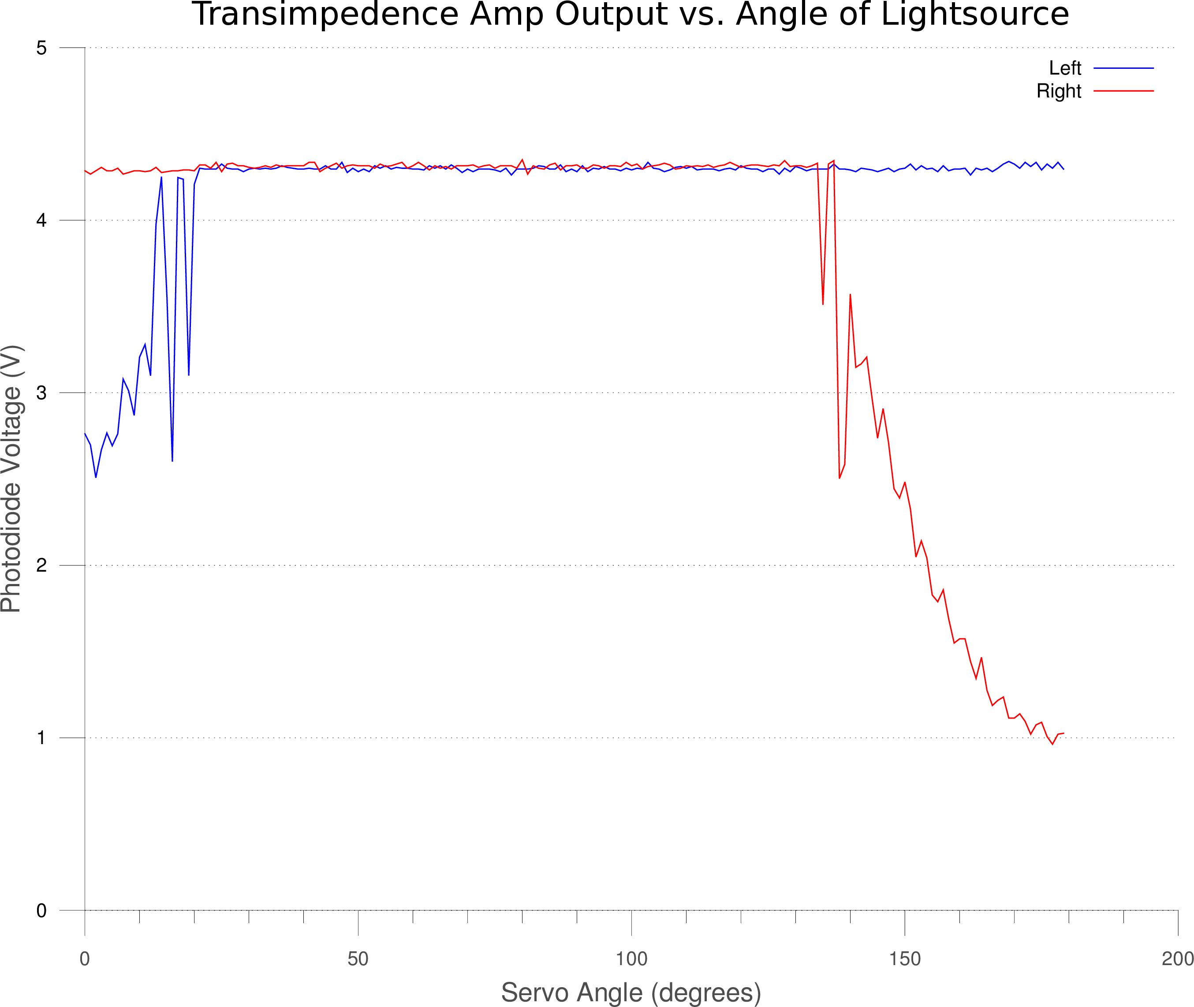
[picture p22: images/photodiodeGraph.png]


### Lab 13

In this lab the robot follows a wall on the right and parks itself in
the second gap ("parking space") it finds. 

1. As per the world file (and see the video for reference), set up 
three blocks, each 50 cm long, with 75 cm gaps between them. In each of the two
gaps, set a block further back. The first column of blocks should be
about 0.8 m from the wall, and the second column should be about 1.2 m
(fairly arbitrary, as long as the robot has space to turn and move into
the "parking space"). If your blocks are too short, that's fine, but
keep the start of the blocks consistent (so the robot just encounters
longer gaps than it expects).
2. Set the robot at one end, load the [localize brain](https://github.com/mitocw/mit-6.01-NarwhalEdu-robot/blob/master/code/swLab13/localizeBrain_narwhal.py), and hit run
3. Robot should proceed until the beginning of the third block, abruptly
   decide where it is, and initiate parking procedure. 
4. Parking procedure: it back up, turn 90 degrees, and move forward into
   the parking spot.

## Debugging

On one Romeo board the analog pin 0 trace was shorted to the analog Vcc pin on the at32u4.  I just ran a razor blade between the two pins a few times.  Check for it if the right IR sensor isn't working correctly.

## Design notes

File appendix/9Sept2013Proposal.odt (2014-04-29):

To: Prof. Isaac Chuang

From: Nancy Ouyang, Cappie Pomeroy (MIT MechE 2013)

Date: 9 September 2013

6.01x Robot Kit Proposal

We propose designing a robot that will:

- Cost $150 in quantity one
- Accept motor voltage levels (be able to drive straight) and output 2 to 3 distance readings at 12 times per second
- Communicate wirelessly with SOAR
- Be wirelessly programmable with up to 40 robots in a single room
- Have a light tracking head that interfaces with existing 6.01 programs to create a light-tracking robot
- Full documentation and release of source files as open source hardware by Dec. 20th

[REDACTED]

Detailed Schedule

12 Weeks

[REDACTED]

1st month deliverable: robot interfacing with SOAR

1. Order parts
2. Parts arrive. 1st iteration robot driving straight (possibly with odometry)
  a. Evaluate and compare CPUs: Beaglebone, Arduino, ARM
  b. Evaluate and compare drive systems: continuous rotation servos, gearmotors
  c. Evaluate and compare odometry systems: rotary encoders, shaft encoders, ir break beam
3. 1st iteration robot outputting accurate distance readings
  a. Evaluate and compare sonar, IR, photoresistor for distance readings
4. 2nd robot iteration for desired features such as ease of assembly

2nd Month deliverable: Light following robot, documentation

5. Light tracking head first iteration
6. Light tracking head communicating with SOAR to create "pet robot" that follows light
7. 2nd iteration of light tracking head for desired features
8. Document robot+light tracking head system

3rd Month deliverable: Wireless robot (two complete systems), documentation

9. Evaluate and compare wireless systems (nRF, xbee, bluetooth) for classroom environment
10. Wirelessly transmit and receive motor voltage levels and distance readings (interface with SOAR)
11. Wireless interface for light tracking head-and-robot system
12. Assemble two complete systems and document system. Release source files under the TAPR open hardware license (http (http://www.tapr.org/OHL):// (http://www.tapr.org/OHL)www (http://www.tapr.org/OHL). (http://www.tapr.org/OHL)tapr (http://www.tapr.org/OHL). (http://www.tapr.org/OHL)org (http://www.tapr.org/OHL)/ (http://www.tapr.org/OHL)OHL (http://www.tapr.org/OHL)) to github or other suitable repository.

Quote

[REDACTED]

Additional Details

[REDACTED]

We will license all our hardware work under the TAPR open hardware license (http (http://www.tapr.org/OHL):// (http://www.tapr.org/OHL)www (http://www.tapr.org/OHL). (http://www.tapr.org/OHL)tapr (http://www.tapr.org/OHL). (http://www.tapr.org/OHL)org (http://www.tapr.org/OHL)/ (http://www.tapr.org/OHL)OHL (http://www.tapr.org/OHL)) to github or other suitable repository, and any software work under GPL.

[REDACTED]

Materials Budget

$1500

Roughly broken down into: $200 express shipping, $600 prototyping one robot and a few partial ones, $400 building two robots, $300 equipment and consumables (wire etc.).

Detailed Prototyping Budget

Sensors | | | Quantity 1
IR sensor | Sharp GP2Y0A02YK0F | https://www.sparkfun.com/products/8958 | 14.95
Short Range IR | Pololu 38kHz range finder | http (http://www.pololu.com/catalog/product/2460):// (http://www.pololu.com/catalog/product/2460)www (http://www.pololu.com/catalog/product/2460). (http://www.pololu.com/catalog/product/2460)pololu (http://www.pololu.com/catalog/product/2460). (http://www.pololu.com/catalog/product/2460)com (http://www.pololu.com/catalog/product/2460)/ (http://www.pololu.com/catalog/product/2460)catalog (http://www.pololu.com/catalog/product/2460)/ (http://www.pololu.com/catalog/product/2460)product (http://www.pololu.com/catalog/product/2460)/2460 (http://www.pololu.com/catalog/product/2460) | 5.95
Sonar Sensor | Maxbotix LVEZ1 | https (https://www.adafruit.com/products/172#Description):// (https://www.adafruit.com/products/172#Description)www (https://www.adafruit.com/products/172#Description). (https://www.adafruit.com/products/172#Description)adafruit (https://www.adafruit.com/products/172#Description). (https://www.adafruit.com/products/172#Description)com (https://www.adafruit.com/products/172#Description)/ (https://www.adafruit.com/products/172#Description)products (https://www.adafruit.com/products/172#Description)/172# (https://www.adafruit.com/products/172#Description)Description (https://www.adafruit.com/pr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 | 24.95
Odometry | EVE-GA1F1724B | http (http://www.digikey.com/product-detail/en/EVE-GA1F1724B/P10859-ND/286883):// (http://www.digikey.com/product-detail/en/EVE-GA1F1724B/P10859-ND/286883)www (http://www.digikey.com/product-detail/en/EVE-GA1F1724B/P10859-ND/286883). (http://www.digikey.com/product-detail/en/EVE-GA1F1724B/P10859-ND/286883)digikey (http://www.digikey.com/product-detail/en/EVE-GA1F1724B/P10859-ND/286883). (http://www.digikey.com/product-detail/en/EVE-GA1F1724B/P10859-ND/286883)com (http://www.digikey.com/product-detail/en/EVE-GA1F1724B/P10859-ND/286883)/ (http://www.digikey.com/product-detail/en/EVE-GA1F1724B/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 | 0.64
Wireless
nRF uC | nRF24L01+ breakout | https (https://www.sparkfun.com/products/691):// (https://www.sparkfun.com/products/691)www (https://www.sparkfun.com/products/691). (https://www.sparkfun.com/products/691)sparkfun (https://www.sparkfun.com/products/691). (https://www.sparkfun.com/products/691)com (https://www.sparkfun.com/products/691)/ (https://www.sparkfun.com/products/691)products (https://www.sparkfun.com/products/691)/691 (https://www.sparkfun.com/products/691) | 19.96
nRF USB | nRF24LU1+ breakout | http (http://www.seeedstudio.com/depot/crazyradio-24ghz-nrf24lu1-usb-radio-dongle-with-antenna-bccr01a-p-1525.html):// (http://www.seeedstudio.com/depot/crazyradio-24ghz-nrf24lu1-usb-radio-dongle-with-antenna-bccr01a-p-1525.html)www (http://www.seeedstudio.com/depot/crazyradio-24ghz-nrf24lu1-usb-radio-dongle-with-antenna-bccr01a-p-1525.html). (http://www.seeedstudio.com/depot/crazyradio-24ghz-nrf24lu1-usb-radio-dongle-with-antenna-bccr01a-p-1525.html)seeedstudio (http://www.seeedstudio.com/depot/crazyradio-24ghz-nrf24lu1-usb-radio-dongle-with-antenna-bccr01a-p-1525.html). (http://www.seeedst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 | 33
Xbee uC | XB24-Z7WIT-004 | http (http://www.digikey.com/product-detail/en/XB24-Z7WIT-004/602-1098-ND/1942304):// (http://www.digikey.com/product-detail/en/XB24-Z7WIT-004/602-1098-ND/1942304)www (http://www.digikey.com/product-detail/en/XB24-Z7WIT-004/602-1098-ND/1942304). (http://www.digikey.com/product-detail/en/XB24-Z7WIT-004/602-1098-ND/1942304)digikey (http://www.digikey.com/product-detail/en/XB24-Z7WIT-004/602-1098-ND/1942304). (http://www.digikey.com/product-detail/en/XB24-Z7WIT-004/602-1098-ND/1942304)com (http://www.digikey.com/product-detail/en/XB24-Z7WIT-004/602-1098-ND/1942304)/ (http://www.digikey.com/prod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 | 17
Xbee USB | XBee Explorer USB + XBee | https (https://www.sparkfun.com/products/8687):// (https://www.sparkfun.com/products/8687)www (https://www.sparkfun.com/products/8687). (https://www.sparkfun.com/products/8687)sparkfun (https://www.sparkfun.com/products/8687). (https://www.sparkfun.com/products/8687)com (https://www.sparkfun.com/products/8687)/ (https://www.sparkfun.com/products/8687)products (https://www.sparkfun.com/products/8687)/8687 (https://www.sparkfun.com/products/8687) | 41.95
Bluetooth uC | BlueSMiRF Silver | https (https://www.sparkfun.com/products/10269):// (https://www.sparkfun.com/products/10269)www (https://www.sparkfun.com/products/10269). (https://www.sparkfun.com/products/10269)sparkfun (https://www.sparkfun.com/products/10269). (https://www.sparkfun.com/products/10269)com (https://www.sparkfun.com/products/10269)/ (https://www.sparkfun.com/products/10269)products (https://www.sparkfun.com/products/10269)/10269 (https://www.sparkfun.com/products/10269) | 39.95
Bluetooth USB | Bluetooth USB 2.0 Micro Adapter Dongle | http (http://www.amazon.com/Bluetooth-USB-Micro-Adapter-Dongle/dp/B001EBE1LI/ref=pd_sxp_f_pt):// (http://www.amazon.com/Bluetooth-USB-Micro-Adapter-Dongle/dp/B001EBE1LI/ref=pd_sxp_f_pt)www (http://www.amazon.com/Bluetooth-USB-Micro-Adapter-Dongle/dp/B001EBE1LI/ref=pd_sxp_f_pt). (http://www.amazon.com/Bluetooth-USB-Micro-Adapter-Dongle/dp/B001EBE1LI/ref=pd_sxp_f_pt)amazon (http://www.amazon.com/Bluetooth-USB-Micro-Adapter-Dongle/dp/B001EBE1LI/ref=pd_sxp_f_pt). (http://www.amazon.com/Bluetooth-USB-Micro-Adapter-Dongle/dp/B001EBE1LI/ref=pd_sxp_f_pt)com (http://www.amazon.com/Bluetooth-USB-Micro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 | 1.55
uC
Arduino | Arduino Leonardo | https (https://www.adafruit.com/products/849):// (https://www.adafruit.com/products/849)www (https://www.adafruit.com/products/849). (https://www.adafruit.com/products/849)adafruit (https://www.adafruit.com/products/849). (https://www.adafruit.com/products/849)com (https://www.adafruit.com/products/849)/ (https://www.adafruit.com/products/849)products (https://www.adafruit.com/products/849)/849 (https://www.adafruit.com/products/849) | 24.95
Beaglebone | BeagleBone Black | https (https://www.adafruit.com/products/1278):// (https://www.adafruit.com/products/1278)www (https://www.adafruit.com/products/1278). (https://www.adafruit.com/products/1278)adafruit (https://www.adafruit.com/products/1278). (https://www.adafruit.com/products/1278)com (https://www.adafruit.com/products/1278)/ (https://www.adafruit.com/products/1278)products (https://www.adafruit.com/products/1278)/1278 (https://www.adafruit.com/products/1278) | 45
ARM | Stellaris LM4F120 LaunchPad | http (http://www.mouser.com/ProductDetail/Texas-Instruments/EK-LM4F120XL/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):// (http://www.mouser.com/ProductDetail/Texas-Instruments/EK-LM4F120XL/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)www (http://www.mouser.com/ProductDetail/Texas-Instruments/EK-LM4F120XL/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). (http://www.mouser.com/ProductDetail/Texas-Instruments/EK-LM4F120XL/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)mouser (http://www.mouser.com/ProductDetail/Texas-Instruments/EK-LM4F120XL/?qs=sGAEpiMZZMsf26MmFqIJrHG9DD2FkafK0BkW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 | 10.99
Chassis
Sain Smart | 4WD Aluminum mobile robot platform | http (http://www.sainsmart.com/sainsmart-4wd-drive-aluminum-mobile-robot-platform-for-robot-arduino-raspberry-pi-gold.html):// (http://www.sainsmart.com/sainsmart-4wd-drive-aluminum-mobile-robot-platform-for-robot-arduino-raspberry-pi-gold.html)www (http://www.sainsmart.com/sainsmart-4wd-drive-aluminum-mobile-robot-platform-for-robot-arduino-raspberry-pi-gold.html). (http://www.sainsmart.com/sainsmart-4wd-drive-aluminum-mobile-robot-platform-for-robot-arduino-raspberry-pi-gold.html)sainsmart (http://www.sainsmart.com/sainsmart-4wd-drive-aluminum-mobile-robot-platform-for-robot-arduino-raspbe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 | 45.99
Robot Mesh | 2WD miniQ | http (http://www.robotmesh.com/2wd-miniq-robot-chassis?gclid=COX8jLOIv7kCFYqZ4Aodcz8AxQ):// (http://www.robotmesh.com/2wd-miniq-robot-chassis?gclid=COX8jLOIv7kCFYqZ4Aodcz8AxQ)www (http://www.robotmesh.com/2wd-miniq-robot-chassis?gclid=COX8jLOIv7kCFYqZ4Aodcz8AxQ). (http://www.robotmesh.com/2wd-miniq-robot-chassis?gclid=COX8jLOIv7kCFYqZ4Aodcz8AxQ)robotmesh (http://www.robotmesh.com/2wd-miniq-robot-chassis?gclid=COX8jLOIv7kCFYqZ4Aodcz8AxQ). (http://www.robotmesh.com/2wd-miniq-robot-chassis?gclid=COX8jLOIv7kCFYqZ4Aodcz8AxQ)com (http://www.robotmesh.com/2wd-miniq-robot-chassis?gclid=COX8jLOIv7kCF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 | 34.3
DFrobot | Turtle-2WD mobile platform | http (http://www.dfrobot.com/index.php?route=product/product&product_id=65):// (http://www.dfrobot.com/index.php?route=product/product&product_id=65)www (http://www.dfrobot.com/index.php?route=product/product&product_id=65). (http://www.dfrobot.com/index.php?route=product/product&product_id=65)dfrobot (http://www.dfrobot.com/index.php?route=product/product&product_id=65). (http://www.dfrobot.com/index.php?route=product/product&product_id=65)com (http://www.dfrobot.com/index.php?route=product/product&product_id=65)/ (http://www.dfrobot.com/index.php?route=product/product&product_id=65)index (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 | 41
Motor Controllers
TI | SN754410NE | http (http://www.mouser.com/ProductDetail/Texas-Instruments/SN754410NE/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):// (http://www.mouser.com/ProductDetail/Texas-Instruments/SN754410NE/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)www (http://www.mouser.com/ProductDetail/Texas-Instruments/SN754410NE/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). (http://www.mouser.com/ProductDetail/Texas-Instruments/SN754410NE/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)mouser (http://www.mouser.com/ProductDetail/Texas-Instruments/SN754410NE/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).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 | 2.34
ST | L298N | http (http://www.digikey.com/product-detail/en/L298N/497-1395-5-ND/585918):// (http://www.digikey.com/product-detail/en/L298N/497-1395-5-ND/585918)www (http://www.digikey.com/product-detail/en/L298N/497-1395-5-ND/585918). (http://www.digikey.com/product-detail/en/L298N/497-1395-5-ND/585918)digikey (http://www.digikey.com/product-detail/en/L298N/497-1395-5-ND/585918). (http://www.digikey.com/product-detail/en/L298N/497-1395-5-ND/585918)com (http://www.digikey.com/product-detail/en/L298N/497-1395-5-ND/585918)/ (http://www.digikey.com/product-detail/en/L298N/497-1395-5-ND/585918)product (http:/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 | 4.67
| | Total | 409.14

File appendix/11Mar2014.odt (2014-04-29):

Table of Contents

Work Log

Work todo

Documentation

SOAR

Bill of Materials

Assembly Instructions

Labs Completion Status

Design Labs

Software Labs

###### Work Log (since 1st meeting with Prof. Chuang)

Assembled a new hardware platform

- Total = $231 ($169 without wireless) in quantity one

Debugged optical encoders ("3.3V" ones work when supplied at 5V…)

Debugged xbee wireless (don't use 115200, make sure to slowly read packets)

Head working (high current op-amp)

Documented our work

###### Work todo

- Enlarge (so that romeo controller can sit between motors) or add third layer to chassis: mount servo head and photodiode, mount full breadboard, mount IR sensors properly without velcro.
- Possibly roll our own board that
  - includes a 2 cell lipo charging circuit
  - is smaller
  - or a PCB chassis
  - add a piezo
  - Easily accessible on/off switches
- Otherwise, lasercut our chassis and IR sensor mounts possibly
- Order servos from factory
- Documentation
- GUI for pioneer to change the port
- Try out 300:1 motors
- A debugging stand (for lab 10 pet robot) -- currently wire spools

###### Documentation

###### SOAR

1. Replace /usr/local/lib/python2.7/dist-packages/soar/outputs/pioneer.py with our pioneer.py
2. Plug in xbee. In a terminal, run dmesg | tail -- it should say something like:

[41246.969987] usb 3-1: FTDI USB Serial Device converter now attached to ttyUSB0

3. sudo gedit /usr/local/lib/python2.7/dist-packages/soar/outputs/pioneer.py and change it to the right port for your connection, e.g.: settings.SERIAL_PORT_NAME = "/dev/ttyUSB0"
  a. If you want to see verbose output for debugging purposes, set debug = True
  b. If not, set debug = skip
4. Run soar
5. Click on Pioneer
  a. If should say P2OS Interface Ready and also denny: battery =
  b. If the button unclicks right away, probably your serial port is incorrect
6. Load a brain
7. Hit the run button

###### Bill of Materials

Name | Total Cost | | Product Name | URL
Lasercut Chassis | 7.95 | pololu | #1507 Pololu 5" Robot Chassis RRC04A Transparent Light-Blue | http (http://www.pololu.com/product/1507):// (http://www.pololu.com/product/1507)www (http://www.pololu.com/product/1507). (http://www.pololu.com/product/1507)pololu (http://www.pololu.com/product/1507). (http://www.pololu.com/product/1507)com (http://www.pololu.com/product/1507)/ (http://www.pololu.com/product/1507)product (http://www.pololu.com/product/1507)/1507 (http://www.pololu.com/product/1507)
Lipo Battery Connector | 0.99 | pololu | JST RCY Plug with 10cm Leads, Male | http (http://www.pololu.com/product/2181):// (http://www.pololu.com/product/2181)www (http://www.pololu.com/product/2181). (http://www.pololu.com/product/2181)pololu (http://www.pololu.com/product/2181). (http://www.pololu.com/product/2181)com (http://www.pololu.com/product/2181)/ (http://www.pololu.com/product/2181)product (http://www.pololu.com/product/2181)/2181 (http://www.pololu.com/product/2181)
Lipo Battery | 4.65 | hobbyking | Turnigy 1000mAh 2S 20C Lipo Pack | http (http://www.hobbyking.com/hobbyking/store/__9170__Turnigy_1000mAh_2S_20C_Lipo_Pack.html):// (http://www.hobbyking.com/hobbyking/store/__9170__Turnigy_1000mAh_2S_20C_Lipo_Pack.html)www (http://www.hobbyking.com/hobbyking/store/__9170__Turnigy_1000mAh_2S_20C_Lipo_Pack.html). (http://www.hobbyking.com/hobbyking/store/__9170__Turnigy_1000mAh_2S_20C_Lipo_Pack.html)hobbyking (http://www.hobbyking.com/hobbyking/store/__9170__Turnigy_1000mAh_2S_20C_Lipo_Pack.html). (http://www.hobbyking.com/hobbyking/store/__9170__Turnigy_1000mAh_2S_20C_Lipo_Pack.html)com (http://www.hobbyking.com/hobbyking/sto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
3x Sharp IR Sensor | 29.85 | pololu | #136 Sharp GP2Y0A21YK0F Analog Distance Sensor 10-80cm | http (http://www.pololu.com/product/136):// (http://www.pololu.com/product/136)www (http://www.pololu.com/product/136). (http://www.pololu.com/product/136)pololu (http://www.pololu.com/product/136). (http://www.pololu.com/product/136)com (http://www.pololu.com/product/136)/ (http://www.pololu.com/product/136)product (http://www.pololu.com/product/136)/136 (http://www.pololu.com/product/136)
3x Sharp IR mount | $15 | robotmesh | Sharp IR Sensor Mounting Bracket-GP2Y0A21/GP2Y0A02YK | http (http://www.robotmesh.com/sharp-ir-sensor-mounting-bracket-gp2y0a21-gp2y0a02yk?___SID=U):// (http://www.robotmesh.com/sharp-ir-sensor-mounting-bracket-gp2y0a21-gp2y0a02yk?___SID=U)www (http://www.robotmesh.com/sharp-ir-sensor-mounting-bracket-gp2y0a21-gp2y0a02yk?___SID=U). (http://www.robotmesh.com/sharp-ir-sensor-mounting-bracket-gp2y0a21-gp2y0a02yk?___SID=U)robotmesh (http://www.robotmesh.com/sharp-ir-sensor-mounting-bracket-gp2y0a21-gp2y0a02yk?___SID=U). (http://www.robotmesh.com/sharp-ir-sensor-mounting-bracket-gp2y0a21-gp2y0a02yk?___SID=U)com (http://www.robotmesh.com/sharp-ir-sens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
2x 100:1 Gearmotor | 33.9 | pololu | #2214 100:1 Micro Metal Gearmotor HP with Extended Motor Shaft | http (http://www.pololu.com/product/2214):// (http://www.pololu.com/product/2214)www (http://www.pololu.com/product/2214). (http://www.pololu.com/product/2214)pololu (http://www.pololu.com/product/2214). (http://www.pololu.com/product/2214)com (http://www.pololu.com/product/2214)/ (http://www.pololu.com/product/2214)product (http://www.pololu.com/product/2214)/2214 (http://www.pololu.com/product/2214)
42x19mm Wheel, pair | 3.85 | robotmesh | Wheel 42x19mm (Pair) | http (http://www.robotmesh.com/wheel-42x19mm-pair):// (http://www.robotmesh.com/wheel-42x19mm-pair)www (http://www.robotmesh.com/wheel-42x19mm-pair). (http://www.robotmesh.com/wheel-42x19mm-pair)robotmesh (http://www.robotmesh.com/wheel-42x19mm-pair). (http://www.robotmesh.com/wheel-42x19mm-pair)com (http://www.robotmesh.com/wheel-42x19mm-pair)/ (http://www.robotmesh.com/wheel-42x19mm-pair)wheel (http://www.robotmesh.com/wheel-42x19mm-pair)-42 (http://www.robotmesh.com/wheel-42x19mm-pair)x (http://www.robotmesh.com/wheel-42x19mm-pair)19 (http://www.robotmesh.com/wheel-42x19mm-pair)mm (http:/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
Extended Motor Bracket, Pair | 2.99 | pololu | #1089 Pololu Micro Metal Gearmotor Bracket Extended Pair | http (http://www.pololu.com/product/1089):// (http://www.pololu.com/product/1089)www (http://www.pololu.com/product/1089). (http://www.pololu.com/product/1089)pololu (http://www.pololu.com/product/1089). (http://www.pololu.com/product/1089)com (http://www.pololu.com/product/1089)/ (http://www.pololu.com/product/1089)product (http://www.pololu.com/product/1089)/1089 (http://www.pololu.com/product/1089)
2x Optical Encoder | 17.9 | pololu | #2591 Optical Encoder Pair Kit for Micro Metal Gearmotors, 3.3V | http (http://www.pololu.com/product/2591):// (http://www.pololu.com/product/2591)www (http://www.pololu.com/product/2591). (http://www.pololu.com/product/2591)pololu (http://www.pololu.com/product/2591). (http://www.pololu.com/product/2591)com (http://www.pololu.com/product/2591)/ (http://www.pololu.com/product/2591)product (http://www.pololu.com/product/2591)/2591 (http://www.pololu.com/product/2591)
2x Caster | $3.8 | Robotmesh | MiniQ Ball Caster Metal | http (http://www.robotmesh.com/ball-caster-metal-miniq):// (http://www.robotmesh.com/ball-caster-metal-miniq)www (http://www.robotmesh.com/ball-caster-metal-miniq). (http://www.robotmesh.com/ball-caster-metal-miniq)robotmesh (http://www.robotmesh.com/ball-caster-metal-miniq). (http://www.robotmesh.com/ball-caster-metal-miniq)com (http://www.robotmesh.com/ball-caster-metal-miniq)/ (http://www.robotmesh.com/ball-caster-metal-miniq)ball (http://www.robotmesh.com/ball-caster-metal-miniq)- (http://www.robotmesh.com/ball-caster-metal-miniq)caster (http://www.robotmesh.com/ball-caster-metal-miniq)-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
3x Standoff | $2 | Robotmesh | 10 sets M3 * 30 nylon standoffs | http (http://www.robotmesh.com/10-sets-m3-30-nylon-standoffs):// (http://www.robotmesh.com/10-sets-m3-30-nylon-standoffs)www (http://www.robotmesh.com/10-sets-m3-30-nylon-standoffs). (http://www.robotmesh.com/10-sets-m3-30-nylon-standoffs)robotmesh (http://www.robotmesh.com/10-sets-m3-30-nylon-standoffs). (http://www.robotmesh.com/10-sets-m3-30-nylon-standoffs)com (http://www.robotmesh.com/10-sets-m3-30-nylon-standoffs)/10- (http://www.robotmesh.com/10-sets-m3-30-nylon-standoffs)sets (http://www.robotmesh.com/10-sets-m3-30-nylon-standoffs)- (http://www.robotmesh.com/10-sets-m3-30-nylon-stand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
7x 3 wire | $6 | Robotmesh | Analog Sensor Cable For Arduino (10 Pack) | http (http://www.robotmesh.com/analog-sensor-cable-for-arduino-10-pack):// (http://www.robotmesh.com/analog-sensor-cable-for-arduino-10-pack)www (http://www.robotmesh.com/analog-sensor-cable-for-arduino-10-pack). (http://www.robotmesh.com/analog-sensor-cable-for-arduino-10-pack)robotmesh (http://www.robotmesh.com/analog-sensor-cable-for-arduino-10-pack). (http://www.robotmesh.com/analog-sensor-cable-for-arduino-10-pack)com (http://www.robotmesh.com/analog-sensor-cable-for-arduino-10-pack)/ (http://www.robotmesh.com/analog-sensor-cable-for-arduino-10-pack)analog (http://www.robotmesh.com/anal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
Romeo controller | $39.9 | Robotmesh | Romeo V2-All in one Controller | http (http://www.robotmesh.com/romeo-v2-all-in-one-controller):// (http://www.robotmesh.com/romeo-v2-all-in-one-controller)www (http://www.robotmesh.com/romeo-v2-all-in-one-controller). (http://www.robotmesh.com/romeo-v2-all-in-one-controller)robotmesh (http://www.robotmesh.com/romeo-v2-all-in-one-controller). (http://www.robotmesh.com/romeo-v2-all-in-one-controller)com (http://www.robotmesh.com/romeo-v2-all-in-one-controller)/ (http://www.robotmesh.com/romeo-v2-all-in-one-controller)romeo (http://www.robotmesh.com/romeo-v2-all-in-one-controller)- (http://www.robotmesh.com/romeo-v2-all-in-on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
Head Servo | $5 | Emax / somewhere
| | | Subtotal | $168.78
Wireless
2x Xbee | 41.9 | Robotmesh | XBee 1mW Trace Antenna - Series 1 (802.15.4) | http (http://www.robotmesh.com/xbee-1mw-trace-antenna-series-1-802-15-4):// (http://www.robotmesh.com/xbee-1mw-trace-antenna-series-1-802-15-4)www (http://www.robotmesh.com/xbee-1mw-trace-antenna-series-1-802-15-4). (http://www.robotmesh.com/xbee-1mw-trace-antenna-series-1-802-15-4)robotmesh (http://www.robotmesh.com/xbee-1mw-trace-antenna-series-1-802-15-4). (http://www.robotmesh.com/xbee-1mw-trace-antenna-series-1-802-15-4)com (http://www.robotmesh.com/xbee-1mw-trace-antenna-series-1-802-15-4)/ (http://www.robotmesh.com/xbee-1mw-trace-antenna-series-1-802-15-4)xbee (http://www.robotmesh.co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
Xbee USB adapter | 18.5 | Robotmesh | XBee USB Adapter V2 | http (http://www.robotmesh.com/xbee-usb-adapter-v2):// (http://www.robotmesh.com/xbee-usb-adapter-v2)www (http://www.robotmesh.com/xbee-usb-adapter-v2). (http://www.robotmesh.com/xbee-usb-adapter-v2)robotmesh (http://www.robotmesh.com/xbee-usb-adapter-v2). (http://www.robotmesh.com/xbee-usb-adapter-v2)com (http://www.robotmesh.com/xbee-usb-adapter-v2)/ (http://www.robotmesh.com/xbee-usb-adapter-v2)xbee (http://www.robotmesh.com/xbee-usb-adapter-v2)- (http://www.robotmesh.com/xbee-usb-adapter-v2)usb (http://www.robotmesh.com/xbee-usb-adapter-v2)- (http://www.robotmesh.com/xbee-usb-adapter-v2)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
USB mini | 1.9 | Robotmesh | Mini USB cable | http (http://www.robotmesh.com/mini-usb-cable):// (http://www.robotmesh.com/mini-usb-cable)www (http://www.robotmesh.com/mini-usb-cable). (http://www.robotmesh.com/mini-usb-cable)robotmesh (http://www.robotmesh.com/mini-usb-cable). (http://www.robotmesh.com/mini-usb-cable)com (http://www.robotmesh.com/mini-usb-cable)/ (http://www.robotmesh.com/mini-usb-cable)mini (http://www.robotmesh.com/mini-usb-cable)- (http://www.robotmesh.com/mini-usb-cable)usb (http://www.robotmesh.com/mini-usb-cable)- (http://www.robotmesh.com/mini-usb-cable)cable (http://www.robotmesh.com/mini-usb-cable)
| | | Total | $236.08

###### Assembly Instructions

See bill of materials for needed parts. Additionally, wire strippers and soldering iron needed.

Motor Unit Assembly

1. Solder optical encoder to gearmotor
2. Tune with oscilloscope and plastic screwdriver (see http (http://www.pololu.com/product/2590):// (http://www.pololu.com/product/2590)www (http://www.pololu.com/product/2590). (http://www.pololu.com/product/2590)pololu (http://www.pololu.com/product/2590). (http://www.pololu.com/product/2590)com (http://www.pololu.com/product/2590)/ (http://www.pololu.com/product/2590)product (http://www.pololu.com/product/2590)/2590 (http://www.pololu.com/product/2590) for more details)
3. Put motor bracket on gearmotor
4. Put wheel on gearmotor

Sensor Unit Assembly

1. Screw IR sensor onto IR mount
2. Swap two wires by cutting, stripping, and soldering them, on the 3-wire analog connector

Servo Head Assembly (not needed in future)

1. Take off bottom part of case4121
2. Desolder control board
3. Resolder 3-wire leads to motor
4. Cut and strip a new 3-wire
5. Solder 3-wire leads to potentiometer
6. Place leads appropriately and put case back on
7. Future: photodiode mount and wiring, servo mount

Robot Assembly

1. Screw motor bracket down to chassis
2. Screw casters onto chassis
3. Screw standoffs to chassis
4. Screw romeo controller to standoffs

Program Xbees

1. Boot into windows and install XCTU
2. Program the xbees to talk to each other (DL and MY commands)
3. Set the baud rate to 19200

Robot Wiring

1. Cut and strip two leads on one of the 3-wires for the motor
2. Plug in / screw leads for motor to M1/M2 and digital pins
3. Plug in IR sensor to analog input pins
4. Plug in Xbee
5. Screw in JST 2-wire XH-style lipo male connector
6. Plug-in battery

###### Labs Completion Status

###### Design Labs

1. Wall Find done http (http://www.youtube.com/watch?v=qMBVbE07Tbg):// (http://www.youtube.com/watch?v=qMBVbE07Tbg)www (http://www.youtube.com/watch?v=qMBVbE07Tbg). (http://www.youtube.com/watch?v=qMBVbE07Tbg)youtube (http://www.youtube.com/watch?v=qMBVbE07Tbg). (http://www.youtube.com/watch?v=qMBVbE07Tbg)com (http://www.youtube.com/watch?v=qMBVbE07Tbg)/ (http://www.youtube.com/watch?v=qMBVbE07Tbg)watch (http://www.youtube.com/watch?v=qMBVbE07Tbg)? (http://www.youtube.com/watch?v=qMBVbE07Tbg)v (http://www.youtube.com/watch?v=qMBVbE07Tbg)= (http://www.youtube.com/watch?v=qMBVbE07Tbg)qMBVbE (http://www.youtube.com/watch?v=qMBVbE07Tbg)07 (http://www.youtube.com/watch?v=qMBVbE07Tbg)Tbg (http://www.youtube.com/watch?v=qMBVbE07Tbg) / ~~Boundary~~ ~~Follow~~~~,~~ ~~bang~~ ~~bang~~ ~~http~~ (http://www.youtube.com/watch?v=XguJQcxj43A)~~://~~ (http://www.youtube.com/watch?v=XguJQcxj43A)~~www~~ (http://www.youtube.com/watch?v=XguJQcxj43A)~~.~~ (http://www.youtube.com/watch?v=XguJQcxj43A)~~youtube~~ (http://www.youtube.com/watch?v=XguJQcxj43A)~~.~~ (http://www.youtube.com/watch?v=XguJQcxj43A)~~com~~ (http://www.youtube.com/watch?v=XguJQcxj43A)~~/~~ (http://www.youtube.com/watch?v=XguJQcxj43A)~~watch~~ (http://www.youtube.com/watch?v=XguJQcxj43A)~~?~~ (http://www.youtube.com/watch?v=XguJQcxj43A)~~v~~ (http://www.youtube.com/watch?v=XguJQcxj43A)~~=~~ (http://www.youtube.com/watch?v=XguJQcxj43A)~~XguJQcxj~~ (http://www.youtube.com/watch?v=XguJQcxj43A)~~43~~ (http://www.youtube.com/watch?v=XguJQcxj43A)~~A~~ (http://www.youtube.com/watch?v=XguJQcxj43A) ~~(~~~~virtual~~~~)~~
2. x
3. n/a
4. x
5. x
6. Boundary Follow Error+Angle (requires re-implementing sonarDist (http://sicp-s4.mit.edu/cat-soop/__STATIC__/6.01_S14/docs/index.html), which relies on 8 sonar readings to calculate angle and distance), Bulls Eye
7. n/a
8. Head with potentiometer http (http://www.youtube.com/watch?v=5r9yhMpieDI):// (http://www.youtube.com/watch?v=5r9yhMpieDI)www (http://www.youtube.com/watch?v=5r9yhMpieDI). (http://www.youtube.com/watch?v=5r9yhMpieDI)youtube (http://www.youtube.com/watch?v=5r9yhMpieDI). (http://www.youtube.com/watch?v=5r9yhMpieDI)com (http://www.youtube.com/watch?v=5r9yhMpieDI)/ (http://www.youtube.com/watch?v=5r9yhMpieDI)watch (http://www.youtube.com/watch?v=5r9yhMpieDI)? (http://www.youtube.com/watch?v=5r9yhMpieDI)v (http://www.youtube.com/watch?v=5r9yhMpieDI)=5 (http://www.youtube.com/watch?v=5r9yhMpieDI)r (http://www.youtube.com/watch?v=5r9yhMpieDI)9 (http://www.youtube.com/watch?v=5r9yhMpieDI)yhMpieDI (http://www.youtube.com/watch?v=5r9yhMpieDI) (position control with motor pot and external pot shown)
9. Head with photodiode http (http://www.youtube.com/watch?v=XeEDuTtJMeo):// (http://www.youtube.com/watch?v=XeEDuTtJMeo)www (http://www.youtube.com/watch?v=XeEDuTtJMeo). (http://www.youtube.com/watch?v=XeEDuTtJMeo)youtube (http://www.youtube.com/watch?v=XeEDuTtJMeo). (http://www.youtube.com/watch?v=XeEDuTtJMeo)com (http://www.youtube.com/watch?v=XeEDuTtJMeo)/ (http://www.youtube.com/watch?v=XeEDuTtJMeo)watch (http://www.youtube.com/watch?v=XeEDuTtJMeo)? (http://www.youtube.com/watch?v=XeEDuTtJMeo)v (http://www.youtube.com/watch?v=XeEDuTtJMeo)= (http://www.youtube.com/watch?v=XeEDuTtJMeo)XeEDuTtJMeo (http://www.youtube.com/watch?v=XeEDuTtJMeo) (mystery right now -- rails to one side if light is not applied)
10. Robot with head -- on hold due to railing of circuit, but seems to work fine
11. x
12. x
13. x
14. Maze

###### Software Labs

1. n/a
2. x
3. x
4. x
5. x
6. x
7. n/a
8. Head circuit
9. Head and robot
10. x
11. n/a
12. x
13. Parking
14. Maze

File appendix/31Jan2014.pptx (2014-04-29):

## NarwhalEdu: 6.01x Contract

1/31/14
Nancy Ouyang
Cappie Pomeroy

## Technical Specs of Proposal

- Cost $150 in quantity one
- Accept motor voltage levels (be able to drive straight) and output 2 to 3 distance readings at 12 times per second
- Communicate wirelessly with SOAR
- Be wirelessly programmable with up to 40 robots in a single room
- Have a light tracking head that interfaces with existing 6.01 programs to create a light-tracking robot

## Current System

Pioneer-DX Robot
University Price: $3,995
Lego Motor: $20 (ebay, used)

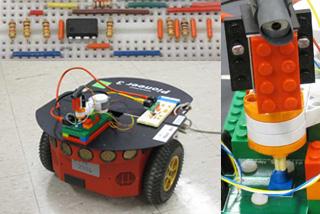
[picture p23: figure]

## Proposed System

A beefier version of the DFRobot MiniQ 2wd (http://www.dfrobot.com/index.php?route=product/product&path=37_111&product_id=555) ($79)
- Quad encoder instead of photodiode, or non-IR encoder
- Sharp IR instead of IR 38 kHz
- (possibly) Better gearmotors
- Lipo instead of 4xAA
Est. $150 in quantity 1
- Wireless (est. +$70)

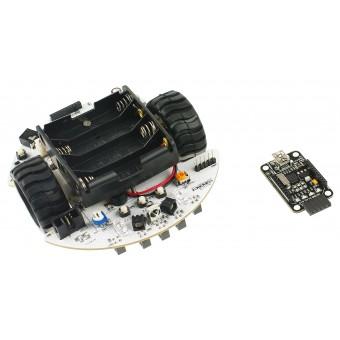
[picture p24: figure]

## Deliverables: Month 1

- Evaluate and compare:
  - CPUs, drive systems, odometry systems, obstacle distance sensors
- 1st iteration robot outputting accurate distance readings

## CPUs

We chose Arduino.
- Arduino: Uno, $25
  - clones for $10
  - sufficient I/O for our purposes
  - free, easy-to-use open source programming toolchain (all OSes)
- Stellaris ARM: $10, but discontinued product line after one month
  - Tiva ARM Replacement: $14
- Beaglebone Black: $45, overkill, expensive

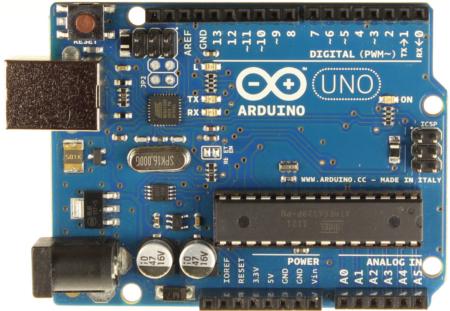
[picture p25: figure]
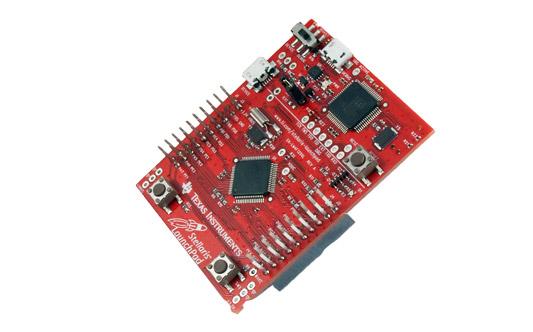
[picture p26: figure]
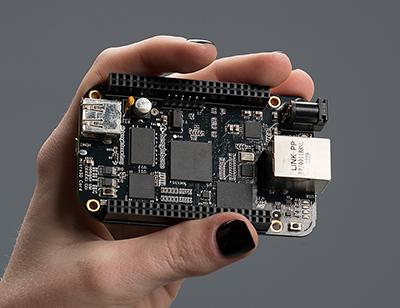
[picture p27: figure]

## Odometry Systems

Rotary Encoders
- Enclosed optical ($.64)
- IR break beam ($2.90)
  - wheel-mounted (low res)
    - 2wd (http://www.dfrobot.com/index.php?route=product/product&product_id=823#.UurQ_UOm2a0), 4wd kit bots
  - motor-mounted

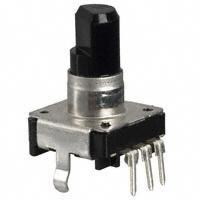
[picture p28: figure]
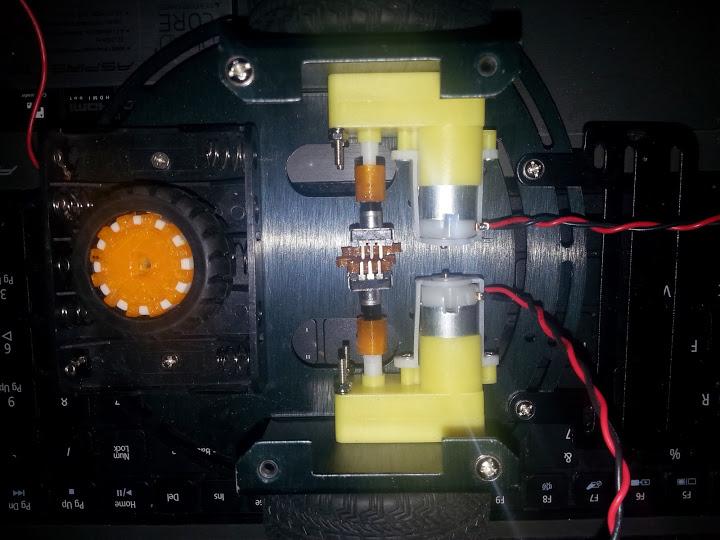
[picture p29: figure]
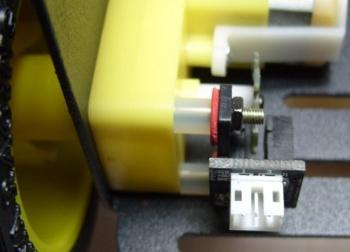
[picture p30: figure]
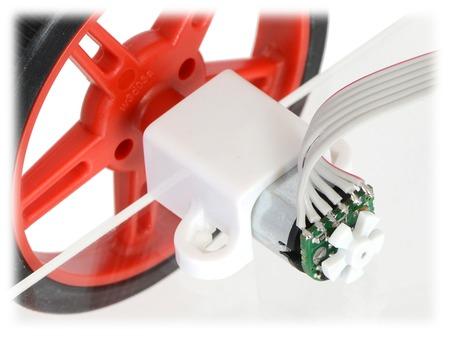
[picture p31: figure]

## Drive/Chassis

- Continuous rotation servos
- Gearmotors
- Sainsmart 4wd
- DFRobot 2wd miniq
- DFRobot Turtle
- Ebay

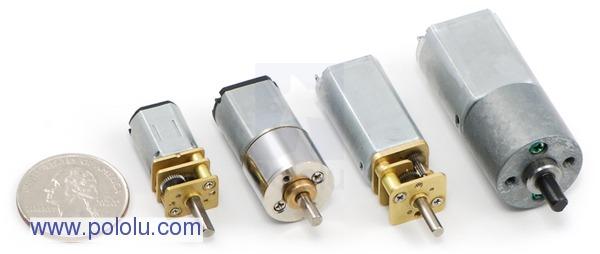
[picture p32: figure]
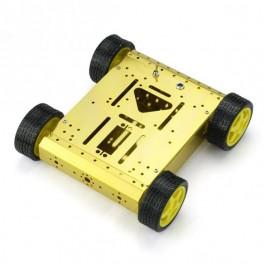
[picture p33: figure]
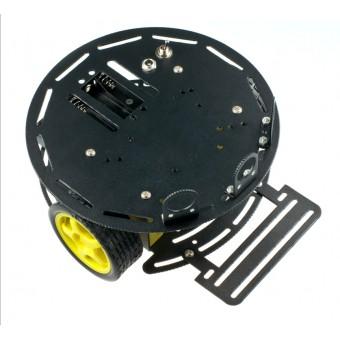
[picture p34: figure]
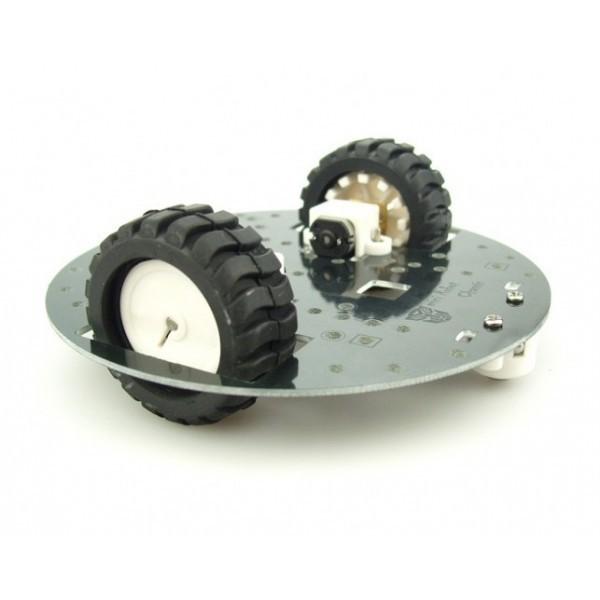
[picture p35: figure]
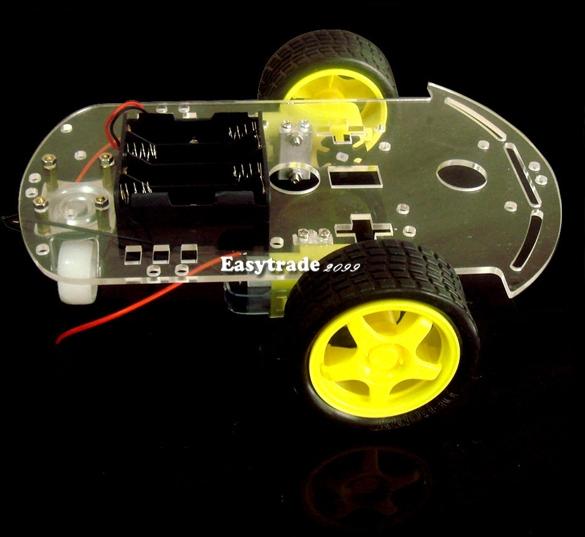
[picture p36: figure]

## Obstacle Distance Readings

- Sonar - expensive ($25)
- Infrared
  - 38 kHz - MiniQ ($8)
    - Designed for proximity, not analog sensing
  - photodiodes ($8)
  - Sharp ($15)
- Photoresistor
  - not fast enough to do modulation

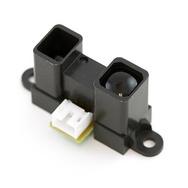
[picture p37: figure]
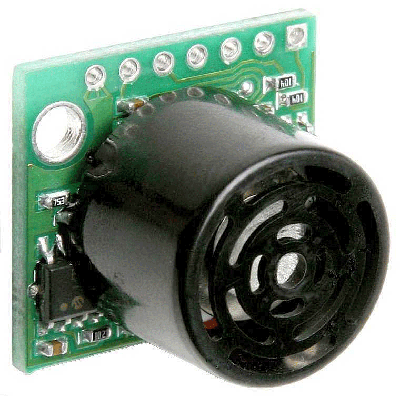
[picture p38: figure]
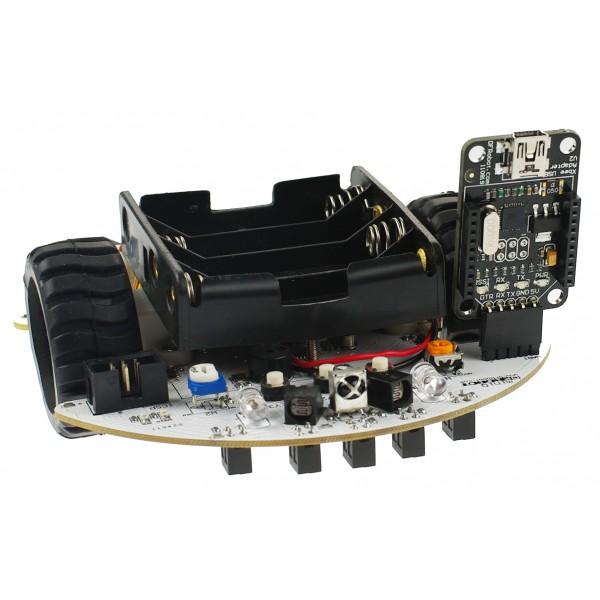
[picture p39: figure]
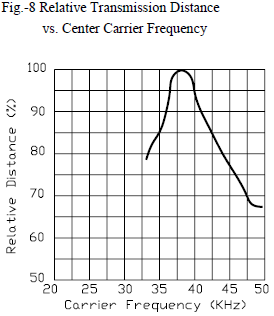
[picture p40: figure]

## Wireless Systems

We found these to be generally unreliable.
- nRF (no program upload, $10)
- Xbee ($70 min.)
- BTBee ($60)
- DFrobot (usb ready program upload, $70)

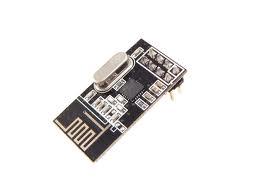
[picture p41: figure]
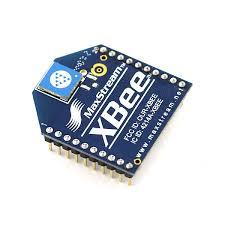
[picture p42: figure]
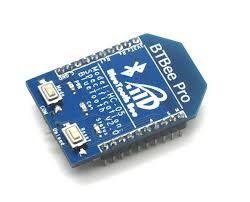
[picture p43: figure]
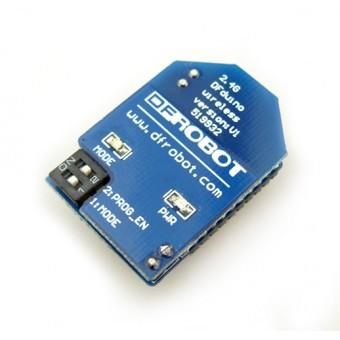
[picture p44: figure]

## Status

- Build robot platform for under $150
- Interface with SOAR
  - Transmit distance readings
  - Move forward and backward
    - Todo: move at specific velocity (important for labs?)

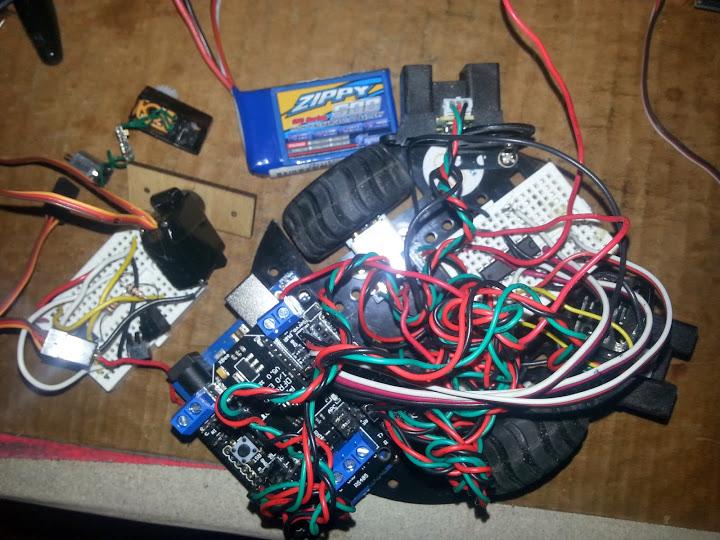
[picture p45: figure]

## Status

- Created servo head
  - Does not operate at 5V system voltage or 7.4V battery voltage with lab circuit (results in ±2.5V)
  - Todo: charge pump or boost converter?

## Todo

- Fix IR encoder dependent on voltage issues
  - Encoder on motor/optical?
- Rotational: Gyro
- Do we need more accurate elapsed position?
- Reliable wireless program uploading and data transmission
Out of scope:
- Turn into manufacturable robot

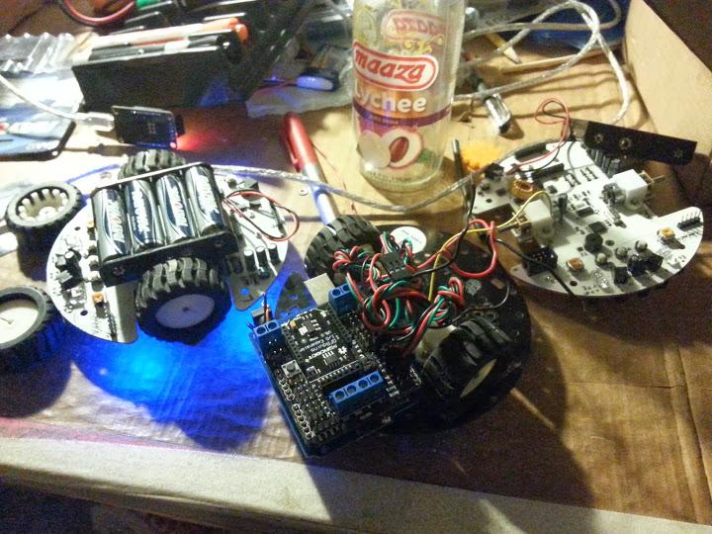
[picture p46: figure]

## Proposed System

Chassis (w/ 2 wheels, motors, 1 castor) | $34.30
encoders x2 | $5.80
ball castors x1 | $1.90
IR sensors GP2Y0A21YK x2 | $30.00
Romeo board | $39.90
Lipo | $5.69
USB cable | $2.50
Sharp IR mounts | $10.00
standoffs | $3.20

Head
Servo | $10.00
Metal servo mounts? | $5.00

Total $148.29


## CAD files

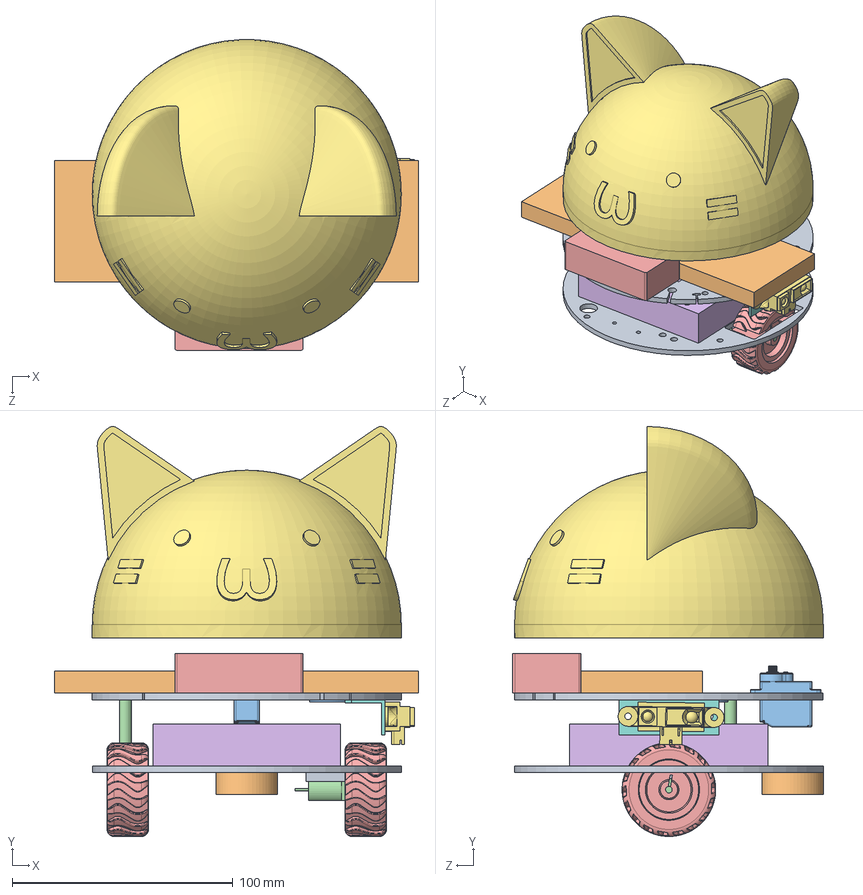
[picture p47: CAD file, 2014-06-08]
hardware/assembly/2LayerRobot-wheelsbottom.SLDASM
165.0 x 185.7 x 140.8 mm

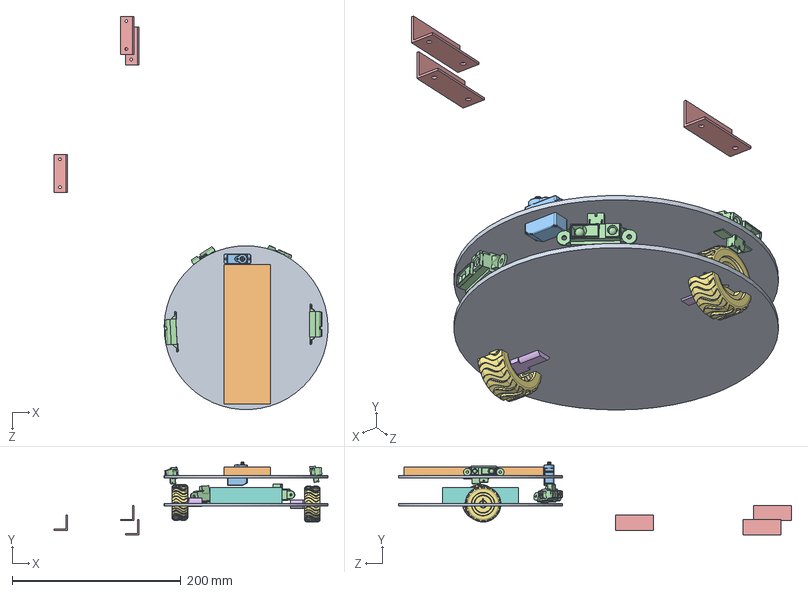
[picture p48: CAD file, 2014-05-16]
hardware/assembly/2LayerRobot.SLDASM
324.3 x 86.0 x 465.5 mm
basecircle x 2
breadboard
Emax ES08A
IR Sensor x 4
IR Sensor Mount x 3
motor x 2
pololu 1.65dia wheel x 2
romeoboard

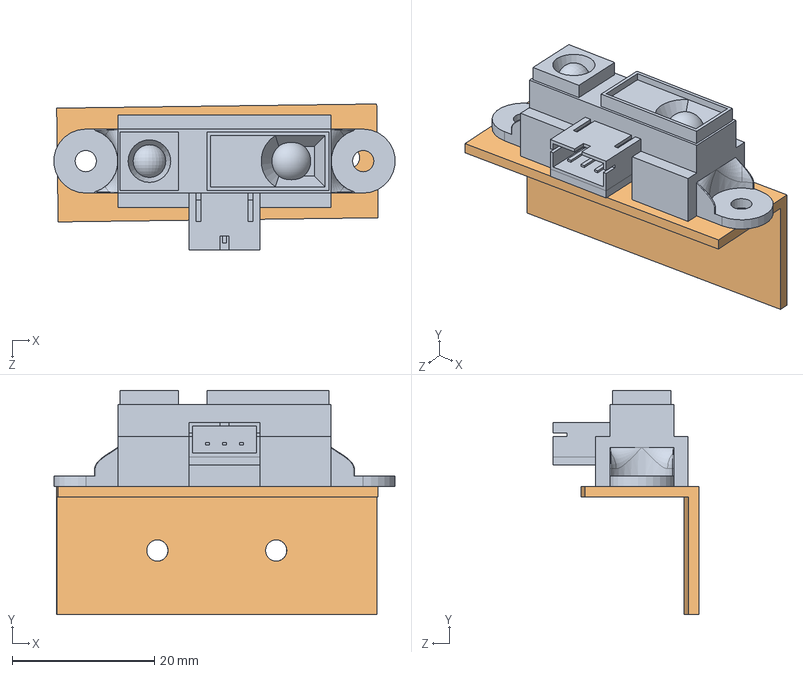
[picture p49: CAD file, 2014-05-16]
hardware/assembly/IRAssembly.SLDASM
47.9 x 31.5 x 20.5 mm
IR Sensor
IR Sensor Mount

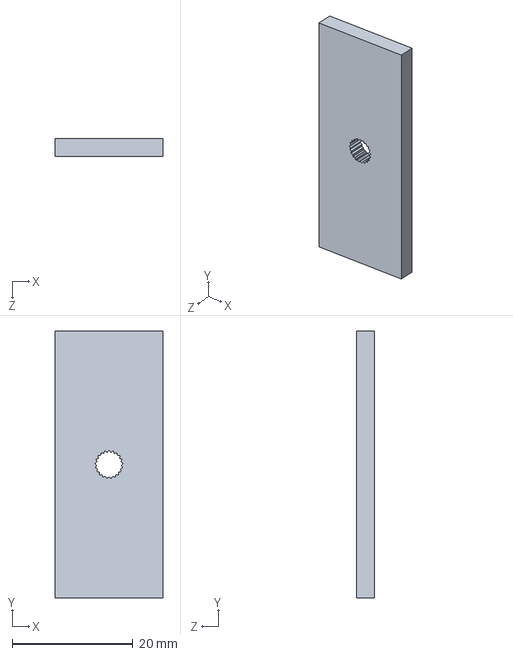
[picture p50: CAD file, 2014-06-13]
hardware/assembly/horn.SLDPRT
17.9 x 44.2 x 3.00 mm

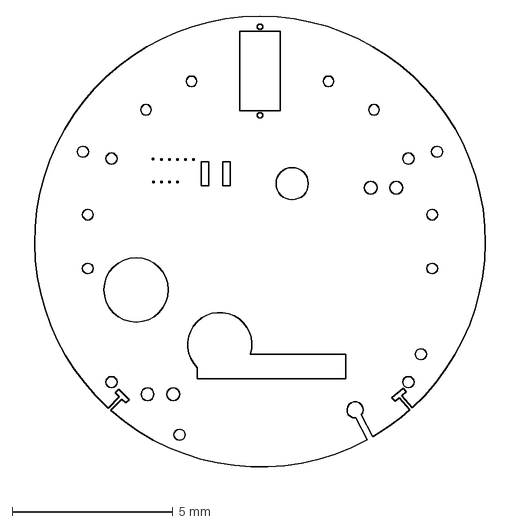
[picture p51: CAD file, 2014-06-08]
hardware/lasercut/top.DXF
15.1 x 14.6 mm

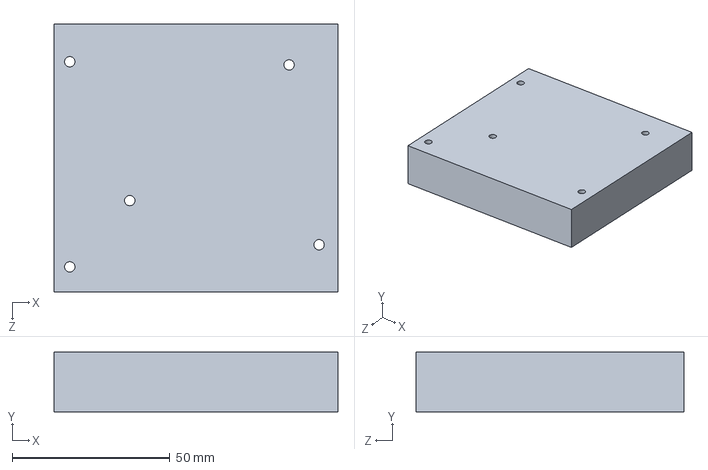
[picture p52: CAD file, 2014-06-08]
hardware/assembly/romeoboard.SLDPRT
90.0 x 19.0 x 85.0 mm

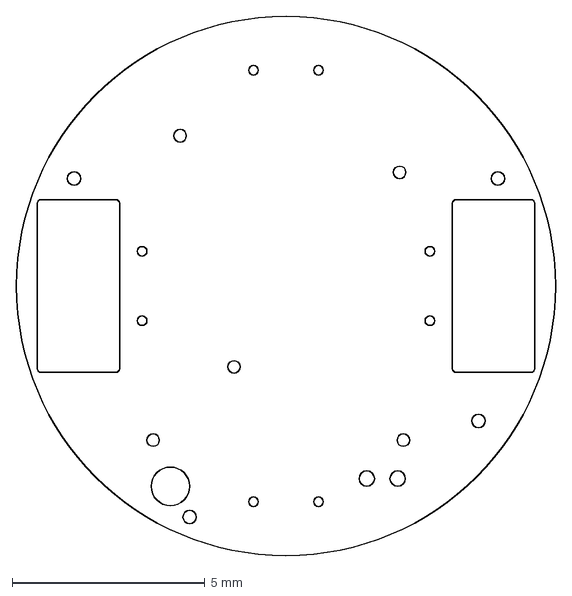
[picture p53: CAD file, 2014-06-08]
hardware/lasercut/bottom.DXF
14.0 x 14.0 mm

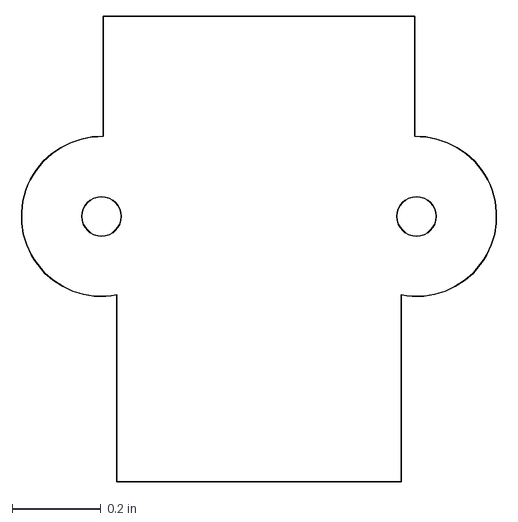
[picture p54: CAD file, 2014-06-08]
hardware/lasercut/MotorShim.DXF
1.09 x 1.05 in

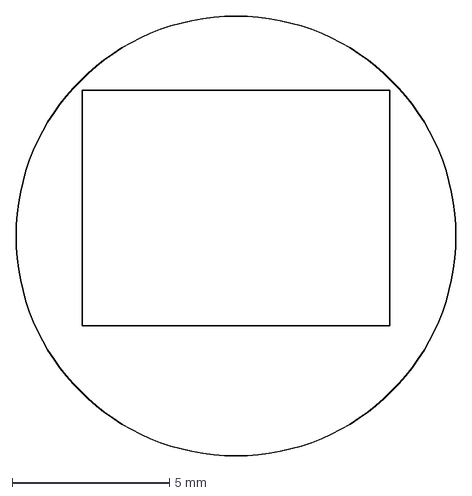
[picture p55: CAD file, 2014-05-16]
hardware/lasercut/hatbase.DXF
14.0 x 14.0 mm

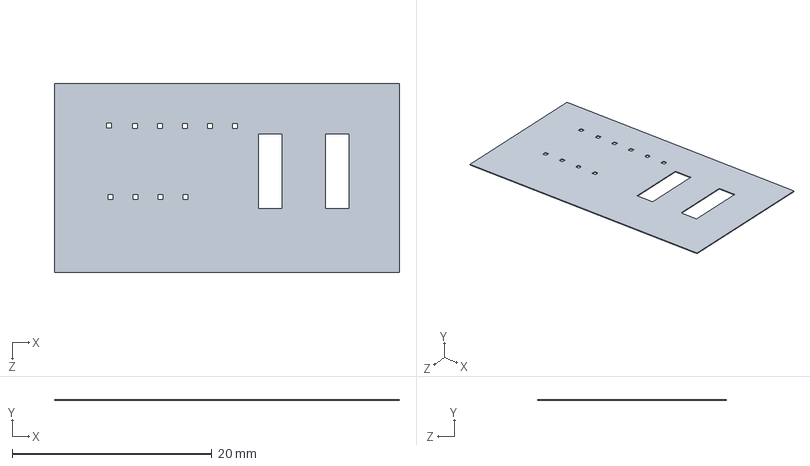
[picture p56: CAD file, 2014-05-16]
hardware/assembly/dummyharness.SLDPRT
34.5 x 0.1 x 18.9 mm

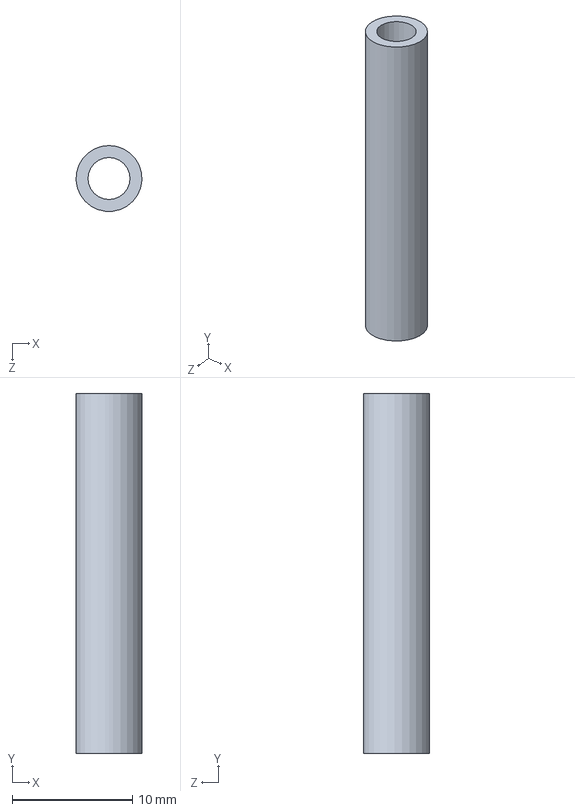
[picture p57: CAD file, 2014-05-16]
hardware/assembly/standoff.SLDPRT
5.49 x 30.0 x 5.50 mm

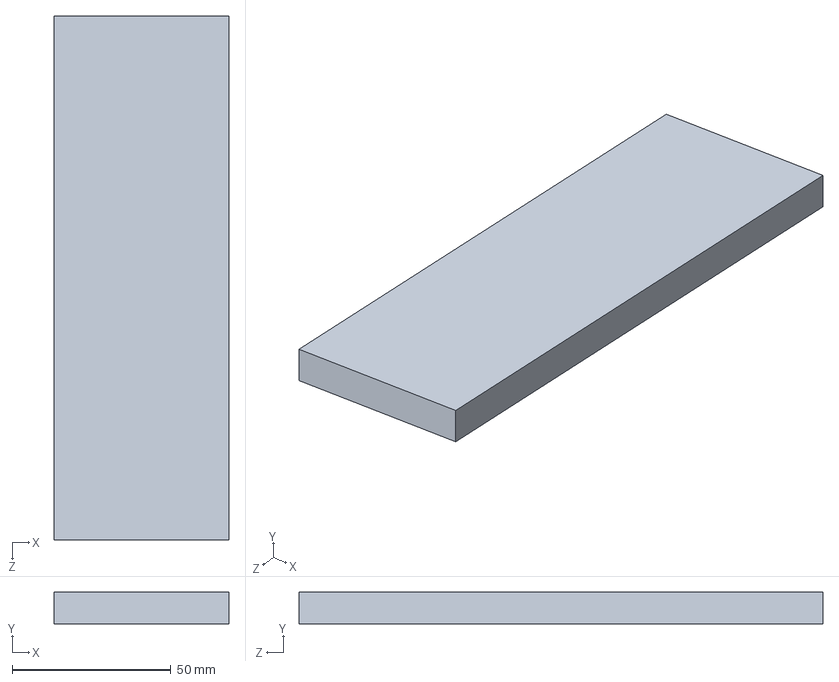
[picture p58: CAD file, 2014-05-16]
hardware/assembly/breadboard.SLDPRT
55.0 x 10.0 x 165.0 mm

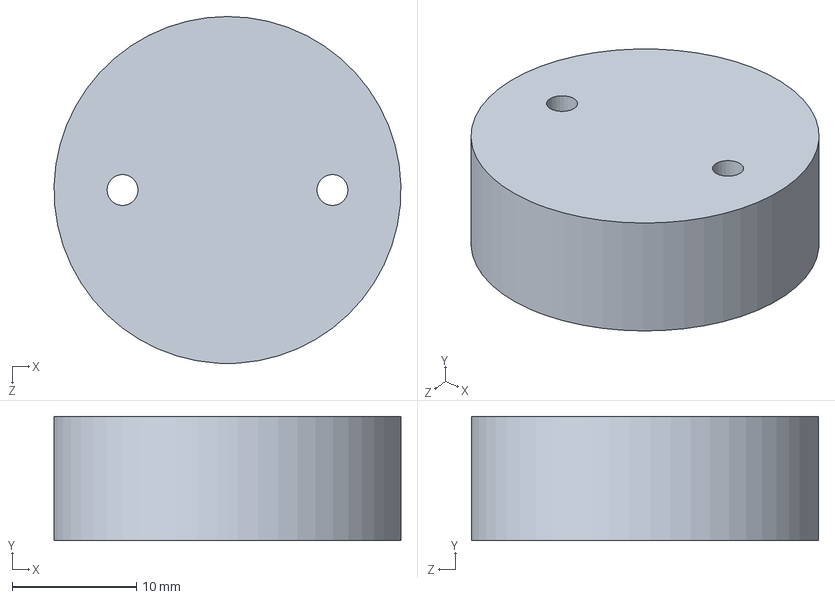
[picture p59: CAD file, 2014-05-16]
hardware/assembly/caster.SLDPRT
27.9 x 10.0 x 27.9 mm

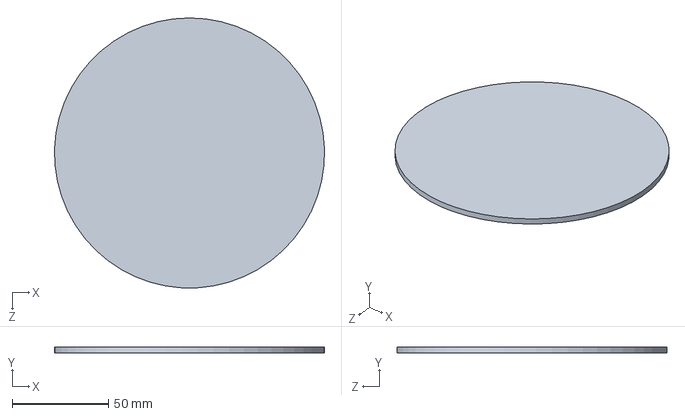
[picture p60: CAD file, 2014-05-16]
hardware/assembly/basecircle.SLDPRT
139.9 x 3.00 x 140.0 mm

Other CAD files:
hardware/assembly/MotorShim.SLDPRT
hardware/assembly/battery.SLDPRT
hardware/assembly/IR Sensor Mount.SLDPRT
hardware/assembly/hatbasehollow.SLDPRT
hardware/assembly/Emax ES08A.SLDPRT
hardware/assembly/IR Sensor.SLDPRT
hardware/assembly/hatbase-blank.sldprt
hardware/assembly/hatbase.STL
hardware/assembly/hatbase.sldprt
hardware/assembly/motor.SLDPRT
hardware/assembly/motorbracket.SLDPRT
hardware/assembly/pololu 1.65dia wheel.SLDPRT
hardware/assembly/wheel.SLDPRT
hardware/assembly/ziptieholes.SLDPRT

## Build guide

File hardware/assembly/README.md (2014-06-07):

5/14/14: Changed top.dxf to fix the hole for upper standoff for hatbase was overlapping with center right IR mount. Other minor fixes.

6/6/14: changed both top and bottom. Moved back right standoff so that there isn't stress on the thin piece between the IR cable holder and battery cable holder.
Created motor standoff based on pololu quadrature PCB layout (http://www.pololu.com/picture/view/0J1454). Need to lasercut out of thin stock (the official ones, which I can't find, are 1.77 mm thick approximately)

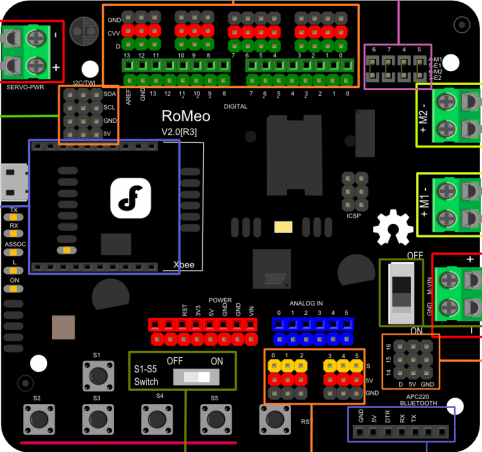
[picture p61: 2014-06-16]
hardware/assembly/Romeo.png

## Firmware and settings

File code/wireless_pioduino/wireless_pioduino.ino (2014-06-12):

// wireless_pioduino.ino -- is the main component of the firmware it is responsible
//   for interpretting and carrying out soar commands, sending SIP packets to soar,
//   and doing various setup routines.
//   contains setup(), loop(), sendSIP(), sendIOSIP(), sendEncoderSIP(), resetAll() 

#include "constants.h"
#include "packethandling.h"
#include "motorcontrol.h"
#include "irsensors.h"
#include "localization.h"
#include <avr/wdt.h>

byte receivedPkt[200];
const int pktHeaderSize = 3;
unsigned int sonarOrder[] = {0,1,2,3};
const int ledPin = 13;

//flags and timers
unsigned long watchdog = 0;
unsigned long sipTime = 0;
boolean connected = false;
boolean SIPFlag = false;
boolean IOFlag = false;
boolean sonarFlag = true;
boolean encoderFlag = false;
boolean motorsEnabled = false;

//default setup function for Arduino runs once at boot
//see http://arduino.cc/en/Reference/Setup
void setup() {
  Serial1.begin(19200);
  //Serial.begin(19200);
  pinMode(ledPin, OUTPUT);
  
  //Initialize PID loops see ./PID_v1.cpp
  leftWheelPID.SetMode(AUTOMATIC);
  leftWheelPID.SetSampleTime(100); 
  leftWheelPID.SetOutputLimits(-255,255);
  leftWheelMeasured = 0;
  leftWheelDesired = 0;
  rightWheelPID.SetMode(AUTOMATIC);
  rightWheelPID.SetSampleTime(100);
  rightWheelPID.SetOutputLimits(-255,255);
  rightWheelMeasured = 0;
  rightWheelDesired = 0;
}

//default loop function for Arduino runs continuously
//see http://arduino.cc/en/Reference/loop
void loop() {
  if(Serial1.available() >= pktHeaderSize) { 
    receivePkt(receivedPkt);
    if(receivedPkt[0] != FAIL) {
      watchdog = millis();

      //SoaR commands are all dealt with using a large switch-case statement.
      if(!connected) {
        byte command = receivedPkt[0];
        byte sndpkt[1];
        switch (command) {
        case SYNC0:
          sndpkt[0] = SYNC0;
          sendPkt(sndpkt, sizeof(sndpkt));
          break;
        case SYNC1:
          sndpkt[0] = SYNC1;
          sendPkt(sndpkt, sizeof(sndpkt));
          break;
        case SYNC2: { //send sync command as well as name of robot, class, and subclass null terminated
          byte SYNC2pkt[] = {SYNC2, 'N', 'Y', 'A', 'N', '!', 0, 'N', 'A', 'R', 'W', 'H', 'A', 'L', 0, 0x41, 0x2B, 0x2B, 0};
          sendPkt(SYNC2pkt, sizeof(SYNC2pkt));
          connected = true;
          digitalWrite(ledPin, HIGH);
          SIPFlag = true;
          break;
        }
        }
      } else { 
        switch (receivedPkt[0]) {
        case PULSE:
          break;
        case OPEN:
          //starts the robot in a clean state turns on white LED
          leftWheelMeasured = 0;
          leftWheelRotational = 0;
          leftWheelLinear = 0;
          leftWheelPID.setITerm(0);
          rightWheelMeasured = 0;
          rightWheelRotational = 0;
          rightWheelLinear = 0;
          rightWheelPID.setITerm(0);
          digitalWrite(ledPin,HIGH);
          break;
        case CLOSE:
          resetAll();
          break;
        case POLLING:
          //change the order of sonar firing or neglect some sonar alters sonarOrder
          for(int i = 0; i < sizeof(sonarOrder)/sizeof(int); i++) {
            sonarOrder[i] = receivedPkt[i+2];
          }
          break;
        case ENABLE:
          //enable or disable the motors (toggles motorsEnabled)
          if(receivedPkt[2] == 1) motorsEnabled = true;
          else {
            motorsEnabled = false;
            setSpeed(rightMtrDirPin, rightMtrSpeedPin, 0);
            setSpeed(leftMtrDirPin, leftMtrSpeedPin, 0);
          }
          break;
        case SETA:
          //set acceleration or deceleration point
          break;
        case SETV:
          //set velocity max speed
          //MAXVEL = receivedPkt[2] | (receivedPkt[3]<<8); //need to alter and map to mm/sec works for now
          break;
        case SETO:
          //reset internal coordinates to 0,0,0. Affects lasth, xpos, and ypos.
          lastTh = 0;
          xpos = 0;
          ypos = 0;
          break;
        case MOVE:
          //translate a distance in mm
          break;
        case ROTATE:
          //rotate an amount in degrees/sec
          break;
        case SETRV:
          //reset max rotation velocity in degrees/sec
          break;
        case VEL:
          //move forward or reverse in mm/sec. Affects leftWheelLinear and rightWheelLinear
          if(motorsEnabled) {
            leftWheelLinear = receivedPkt[2] | (receivedPkt[3]<<8);
            if(receivedPkt[1] == 0x1B) { //check for negative integers
              leftWheelLinear = -leftWheelLinear;
            }
            rightWheelLinear = leftWheelLinear;
            drive();
          }
          break;
        case HEAD:
          //turn to absolute heading counterclockwise in degrees
          break;
        case DHEAD:
          //turn relative to current heading counterclockwise in degrees
          break;
        case SAY:
          //control a pieazo?
          break;
        case JOYREQUEST:
          //request one (1), a continuous stream (>1), or stop (0) joystick SIPs
          break;
        case CONFIG:
          //send a configuration SIP
          break;
        case ENCODER: {
          //request encoder reading (1), or stream (>1), or stop sending readings(0). Toggles encoderFlag
          int argument = receivedPkt[2] | receivedPkt[3]<<8;
          if(argument == 0) {
            encoderFlag = false;
          } else if(argument == 1) {
            sendEncoderSIP();
          } else if(argument > 1) {
            sendEncoderSIP();
            encoderFlag = true;
          }
          break;
        }
        case RVEL: {
          //rotate in degrees per second.  Alters leftWheelRotational and rightWheelRotational.
          if(motorsEnabled) {
            int rvel = receivedPkt[2] | (receivedPkt[3]<<8);
            //check for negative integers
            if(receivedPkt[1] == 0x1B) {
              leftWheelRotational = -rvel;
              rightWheelRotational = rvel;
            } else {
              leftWheelRotational = rvel;
              rightWheelRotational = -rvel;
            }
            drive();
          }
          break;
        }
        case DCHEAD:
          //heading setpoint relative to last setpoint
          break;
        case SETRA:
          //set rotational acceleration
          break;
        case SONAR:
          //send 0 to disable all sonar or 1 to enable them. Toggles sonarFlag
          if(receivedPkt[2]&0x01 == 1) sonarFlag = true;
          else sonarFlag = false;
          //pioneer has four arrays I only care about the one hence the &0x01
          break;
        case STOP:
          //stop moving motors stay enabled.  Affects leftWheelDesired and rightWheelDesired
          if(motorsEnabled) {
            leftWheelDesired = 0;
            rightWheelDesired = 0;
            drive();
          }
          break;
        case DIGOUT:
          //Msbits is a byte mask that selects output port(s) for changes; lsbits set (1) or reset (0) the selected port.
          break;
        case VEL2:
          //set independant wheel velocities LSB=right; MSB=left
          break;
        case GRIPPER:
          break;
        case ADSEL:
          //set the A/D port number to be used in the SIP
          break;
        case GRIPPERVAL:
          //gripper server values
          break;
        case GRIPREQUEST:
          //Request one, a continuous stream (>1), or stop (0)Gripper SIPs.
          break;
        case IOREQUEST: {
          //request 1, a continuous stream of SIPs (>1), or stop (0). Toggles IOFlag
          int argument = receivedPkt[2] | receivedPkt[3]<<8;
          if(argument == 0) {
            IOFlag = false;
          } else if(argument == 1) {
            sendIOSIP();
          } else if(argument > 1) {
            sendIOSIP();
            IOFlag = true;
          }
          break;
        }
        case TTY2:
          //Send string argument to serial device on AUX port on uC
          break;
        case GETAUX:
          //Request to retrieve 1-200 bytes from the aux serial channel; 0 flushes the aux serial input buffer.
          break;
        case BUMPSTALL:
          //Stop and register a stall if front (1), rear (2) or either (3) bump-ring contacted. Off (default) is 0.
          break;
        case TCM2:
          //TCM2 module commands??
          break;
        case JOYDRIVE:
          //allow (1) or deny (0) joystick control
          break;
        case SONARCYCLE:
          //Change the sonar cycle time; in milliseconds
          break;
        case HOSTBAUD:
          //Change the HOST serial port baud rate to 0=9600, 1=19200, 2=38400, 3=57600, or 4=115200.
          break;
        case AUX1BAUD:
          //Change the AUX1 serial port baud rate (see HOSTBAUD).
          break;
        case AUX2BAUD:
          //Change the AUX2 serial port baud rate (see HOSTBAUD).
          break;
        case AUX3BAUD:
          //Change the AUX3 serial port baud rate (see HOSTBAUD).
          break;
        case E_STOP:
          //emergency stop overrides deceleration
          setSpeed(rightMtrDirPin, rightMtrSpeedPin, 0);
          setSpeed(leftMtrDirPin, leftMtrSpeedPin, 0);
          break;
        case M_STALL:
          //Argument 1=MOTORS button off causes a stall
          break;
        case GYROREQUEST:
          //Request one, a continuous stream (>1), or stop (0) Gyro SIPs.
          break;
        case LCDWRITE:
          //there is no LCD screen on our robot lol
          break;
        case TTY4:
          break;
        case GETAUX3:
          break;
        case TTY3:
          break;
        case GETAUX2:
          break;
        case CHARGE:
          //0=release; 1=deploy autocharge-docking mechanism.
          break;
        case RESET:
          //Force a power on-like reset of the microcontroller.
          cli();                  // Clear interrupts
          wdt_enable(WDTO_15MS);  // Set the Watchdog to 15ms
          while(1);               // Enter an infinite loop
          break;
        case MAINTENANCE:
          //Engage microcontroller maintenance (ARSHstub) mode.
          break;
        default:
          break;
        }
      }
    }
  }
  if(millis() - sipTime > 100 && connected) { //soar expects SIPs every 100ms or so
    calculatePosition();
    if(SIPFlag) {
      int sonarValues[sizeof(sonarOrder)/sizeof(int)];
      if(!sonarFlag) memset(sonarValues,0,sizeof(sonarValues)/sizeof(int));
      else {
        for(int i = 0; i < sizeof(sonarValues)/sizeof(int); i++) {sonarValues[i] = getIRValue(sonarOrder[i]);
        }
      }
      sendSIP(sonarOrder,sonarValues,sizeof(sonarValues)/sizeof(int));
    }
    if(motorsEnabled) drive(); //update PID
    if(encoderFlag) sendEncoderSIP();
    if(IOFlag) sendIOSIP();
    sipTime = millis();
  }
  //If there hasn't been a SoaR command for > 2 seconds we're probably disconnected
  if((millis() - watchdog) > 2000) {
    resetAll();
  }
}

/* Constructs and sends the Server Information Packet
   argumens: number of sonar readings being sent.
   much smaller than the original SIP only location
   and sonar data is sent see pg. 30 code/pioneer-manualv3.pdf*/
void sendSIP(unsigned int sonarDiscs[], int sonarReadings[], size_t sonarCount) {
  byte SIPpkt[8+3*sonarCount];
  SIPpkt[0] = 0x32 | motorsEnabled;
  SIPpkt[1] = (int)xpos&0xFF;
  SIPpkt[2] = (int)xpos>>8;
  SIPpkt[3] = (int)ypos&0xFF;
  SIPpkt[4] = (int)ypos>>8;
  SIPpkt[5] = (int)thpos&0xFF;
  SIPpkt[6] = (int)thpos>>8;
  SIPpkt[7] = sonarCount&0xFF;
  for(int i=0; i < sonarCount; i++) {
    SIPpkt[8+i*3] = sonarDiscs[i];
    SIPpkt[9+i*3] = sonarReadings[i]&0xFF;
    SIPpkt[10+i*3] = sonarReadings[i]>>8;
  }
  sendPkt(SIPpkt, sizeof(SIPpkt));
}

/* Constructs and sends the IOSIP packet it only contains
   values for 3 analog pins, the rest are blank.  The blank
   ones are left in in case more analog readings are desired
   so that it will be a simple change. It is also smaller than
   the one from original pioneer OS. */
void sendIOSIP() {
  byte IOSIPpkt[17];
  int leftPhotodiode = analogRead(A4); 
  int rightPhotodiode = analogRead(A5); 
  int servoPotVoltage = analogRead(A10);
  int analog11 = analogRead(A11);
  IOSIPpkt[0] = 0xF0; //packet type always 0xF0
  IOSIPpkt[1] = 0; //Analog port values resolution 0-1023 two bytes!, 0-5 VDC
  IOSIPpkt[2] = 0;
  IOSIPpkt[3] = 0;
  IOSIPpkt[4] = 0;
  IOSIPpkt[5] = 0;
  IOSIPpkt[6] = 0;
  IOSIPpkt[7] = 0;
  IOSIPpkt[8] = 0;
  IOSIPpkt[9] = servoPotVoltage&0xFF;
  IOSIPpkt[10] = servoPotVoltage>>8; 
  IOSIPpkt[11] = leftPhotodiode&0xFF;
  IOSIPpkt[12] = leftPhotodiode>>8;
  IOSIPpkt[13] = rightPhotodiode&0xFF;
  IOSIPpkt[14] = rightPhotodiode>>8;
  IOSIPpkt[15] = analog11&0xFF;
  IOSIPpkt[16] = analog11>>8;
  sendPkt(IOSIPpkt, sizeof(IOSIPpkt));
}

/* Constructs and sends the Encoder SIP
   see pg. 38 code/pioneer-robotv3.pdf */
void sendEncoderSIP() {
  byte encoderSIP[5];
  encoderCountRight = -rightEncoder.read();
  encoderCountLeft = leftEncoder.read();
  encoderSIP[0] = 0x90;
  encoderSIP[1] = encoderCountLeft&0xFF;
  encoderSIP[2] = encoderCountLeft>>8;
  encoderSIP[3] = encoderCountRight&0xFF;
  encoderSIP[4] = encoderCountRight>>8;
}

/* Returns the robot to a state similar to a just booted state
   all speeds, flags, encoders, and positions are set to
   zero */
void resetAll() {
  //left motor
  setSpeed(leftMtrDirPin, leftMtrSpeedPin, 0);
  leftWheelMeasured = 0;
  leftWheelRotational = 0;
  leftWheelLinear = 0;
  leftWheelPID.setITerm(0);
  lastEncoderCountLeft = 0;
  encoderCountLeft = 0;
  leftEncoder.write(0);

  //right motor
  setSpeed(rightMtrDirPin, rightMtrSpeedPin, 0);
  rightWheelMeasured = 0;
  rightWheelRotational = 0;
  rightWheelLinear = 0;
  rightWheelPID.setITerm(0);
  lastEncoderCountRight = 0;
  encoderCountRight = 0;
  rightEncoder.write(0);

  //flags
  motorsEnabled = false;
  encoderFlag = false;
  IOFlag = false;
  SIPFlag = false;
  connected = false;

  //position
  lastTh = 0;
  xpos = 0;
  ypos = 0;

  digitalWrite(ledPin, LOW);
  return;
}

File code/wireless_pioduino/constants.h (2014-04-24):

/* constants.h -- contains all of the soar commands and their values */
#include "Arduino.h"

const byte SYNC0 = 0;
const byte SYNC1 = 1;
const byte SYNC2 = 2;

//Argument types
const byte  ARGINT		= 0x3B;
const byte  ARGNINT		= 0x1B;
const byte  ARGSTR		= 0x2B;

// P2OS Commands
const byte PULSE				=   0;
const byte OPEN					=   1;
const byte CLOSE				=   2;
const byte POLLING				=   3;
const byte ENABLE				=   4;
const byte SETA					=   5;
const byte SETV					=   6;
const byte SETO					=   7;
const byte MOVE					=   8;
const byte ROTATE				=   9;
const byte SETRV				=  10;
const byte VEL					=  11;
const byte HEAD					=  12;
const byte DHEAD				=  13;
const byte SAY					=  15;
const byte JOYREQUEST				=  17;
const byte CONFIG				=  18;
const byte ENCODER				=  19;
const byte RVEL					=  21;
const byte DCHEAD				=  22;
const byte SETRA				=  23;
const byte SONAR				=  28;
const byte STOP					=  29;
const byte DIGOUT				=  30;
const byte VEL2					=  32;
const byte GRIPPER				=  33;
const byte ADSEL				=  35;
const byte GRIPPERVAL				=  36;
const byte GRIPREQUEST				=  37;
const byte IOREQUEST				=  40;
const byte TTY2					=  42;
const byte GETAUX				=  43;
const byte BUMPSTALL				=  44;
const byte TCM2					=  45;
const byte JOYDRIVE				=  47;
const byte SONARCYCLE				=  48;
const byte HOSTBAUD				=  50;
const byte AUX1BAUD				=  51;
const byte AUX2BAUD				=  52;
const byte AUX3BAUD				=  53;
const byte E_STOP				=  55;
const byte M_STALL				=  56;
const byte GYROREQUEST				=  58;
const byte LCDWRITE				=  59;
const byte TTY4					=  60;
const byte GETAUX3				=  61;
const byte TTY3					=  66;
const byte GETAUX2				=  67;
const byte CHARGE				=  68;
const byte RESET				= 254;
const byte MAINTENANCE				= 255;
const byte FAIL                                 = 253;

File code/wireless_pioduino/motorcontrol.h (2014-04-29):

/* motorcontrol.h -- handles the motors, encoders, and velocity outputs
   contains setSpeed() and drive() */
#include "Encoder.h"
#include "PID_v1.h"

//motor pins
const int rightMtrSpeedPin = 5;
const int leftMtrSpeedPin = 6;
const int rightMtrDirPin = 4;
const int leftMtrDirPin = 7;

//Encoder setup
//each encoder must have one interrupt enabled pin see ./Encoder.h
Encoder rightEncoder(2, 8); 
Encoder leftEncoder(3, 9);
int32_t encoderCountRight = 0;
int32_t encoderCountLeft = 0;
int32_t lastEncoderCountRight = 0;
int32_t lastEncoderCountLeft = 0;

//PID setup
const double kp = 0.3;
const double ki = 2.2;
const double kd = 0.002; 
double leftWheelDesired = 0;
double leftWheelMeasured = 0;
double leftWheelControl = 0;
double leftWheelRotational = 0;
double leftWheelLinear = 0;
double rightWheelDesired = 0;
double rightWheelMeasured = 0;
double rightWheelControl = 0;
double rightWheelRotational = 0;
double rightWheelLinear = 0;
PID leftWheelPID(&leftWheelMeasured, &leftWheelControl, &leftWheelDesired, kp, ki, kd, DIRECT);
PID rightWheelPID(&rightWheelMeasured, &rightWheelControl, &rightWheelDesired, kp, ki, kd, DIRECT);

//conversion factors and calculation values
const int wheelDiameter = 42;
const int ticksPerRev = 5960; //2000 for 100:1, 5960 for 298:1
const int velocityConvFactor = PI*wheelDiameter*1000;
unsigned long previousTime = 0;
unsigned long currentTime = 0;
float rightEncoderDelta = 0;
float leftEncoderDelta = 0;
/* 320RPM MOTOR: 320RPM @ 6v, so say 300 RPM at 5v = 5 rev/sec, 2000 ticks/rev of output shaft, = 10000 ticks/sec
   255/10000 = 0.0255 conversion factor for seconds * 1000 25.5 conversion factor ms */
float soarPWMConvFactor = 28.5;

/* writes PWM commands to the motors takes a motor control pin, a motor
    direction pin, and a speed.  Negative speed means drive backwards. */
void setSpeed(int direction, int control, int speed) {
  if(speed < 0) {
    digitalWrite(direction, LOW);
  } else digitalWrite(direction, HIGH);
  analogWrite(control, abs(speed));
}

/* Determines wheel velocities from encoder counts and runs the PID loop */
void drive() {
  leftWheelDesired = leftWheelLinear + leftWheelRotational;
  rightWheelDesired = rightWheelLinear + rightWheelRotational;
  currentTime = millis();
  double dT = (currentTime - previousTime);
  
  //The encoder counts are mirrored because they're on oposite sides.
  //One could also switch pins in the Encoder declaration, but this seems more intuitive.
  encoderCountRight = -rightEncoder.read();
  encoderCountLeft = leftEncoder.read();
  rightEncoderDelta = encoderCountRight - lastEncoderCountRight;
  leftEncoderDelta = encoderCountLeft - lastEncoderCountLeft;
  lastEncoderCountRight = encoderCountRight;
  lastEncoderCountLeft = encoderCountLeft;
  rightWheelMeasured = (rightEncoderDelta/dT)*soarPWMConvFactor;
  leftWheelMeasured = (leftEncoderDelta/dT)*soarPWMConvFactor;

  //refresh *WheelOuputs see ./PID_v1.cpp
  leftWheelPID.Compute();
  rightWheelPID.Compute();
  setSpeed(rightMtrDirPin, rightMtrSpeedPin, rightWheelControl);
  setSpeed(leftMtrDirPin, leftMtrSpeedPin, leftWheelControl);
  previousTime = currentTime;
}

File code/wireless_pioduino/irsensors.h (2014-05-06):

/* irsensors.h -- interacts with all of the IR sensors
   contains getIRValue(), readIR() */
#define leftIRPin 0
#define centerLeftIRPin 1
#define centerRightIRPin 2
#define rightIRPin 3
const float voltConvFactor = 5.0/1024;
// worked out from figure 2 in gp2y0a21yk0f.pdf
const float delta = 10*(80-10)/2;

/* Reads 5 voltages from the IR pins and averages them to
   find the distance from the object being observed.  Takes
   an int for the pin an IR sensor is on and returns the
   distance measurement as an int */
int getIRValue(int IRpin) {
  float IRVolts = 0.0;
  float distance = 0.0;
  float samples = 5.0;
  for(int i=0; i<samples ;i++) {
    IRVolts = analogRead(IRpin)* voltConvFactor;
    distance += delta*pow(IRVolts, -1.10); // theoretical distance / (1/Volts)S
  }
  distance = distance/samples; //average
  return((int)(distance)); // print the distance in mm
}

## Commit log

2014-04-24 added wireless_pioduino code
2014-04-25 added Arduino section still needs screenshots
2014-05-06 altered code/ for 4 ir sensors
2014-05-06 added copy of lib601.tar.gz and fixed link in instructions
    [wireless_pioduino.ino]
2014-05-06 changed radii to match new version, fixed lab sonar numbers
    [localization.h]
2014-05-16 added solidworks and lasercutting files, svg sources for images in documentation
    [2LayerRobot-wheelsbottom.SLDASM, 2LayerRobot.SLDASM, Emax ES08A.SLDPRT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]
2014-06-07 updated top and bottom plates to avoid cracking, added readme, motorshim dxf
    [2LayerRobot-wheelsbottom.SLDASM, 2LayerRobot.SLDASM, Emax ES08A.SLDPRT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]
2014-06-08 moved caster, slot for motor terminal blocks
    [2LayerRobot-wheelsbottom.SLDASM, MotorShim.DXF, MotorShim.SLDPRT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]
2014-06-12 fixed angle brain sonar values
    [test_ino.ino, wireless_pioduino.ino]
2014-06-13 update docs
    [horn.SLDPRT]
2014-06-13 added lasercutting instructions
2014-06-16 added shorted traces bit
